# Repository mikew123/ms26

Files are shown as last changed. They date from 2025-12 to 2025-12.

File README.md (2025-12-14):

# ms26
Mini Sumo DIY for Spring 2026 RoboRama.<br>
This is a DIY mini sumo 10cmx10cm robot made with 3D printed body with mounts and "off the shelf" modules and a point to point wired 0.1" bread board to connect it all together.<br>

# Mechanics
## Body
The body is in 2 parts printed on 3D printer, a main body and a top lid and is created using Matte Black PLA filiment.<br>
The main body is one piece and has mounts for the motors/wheels and the circuit board and sensors. There is an opening on the side for the battery to be inserted.<br>
The top lid bolts onto the body and has compartments to put pennys in as weights, there is also a cover to tightly hold the pennys in place.<br>
3D design using FreeCad:<br>
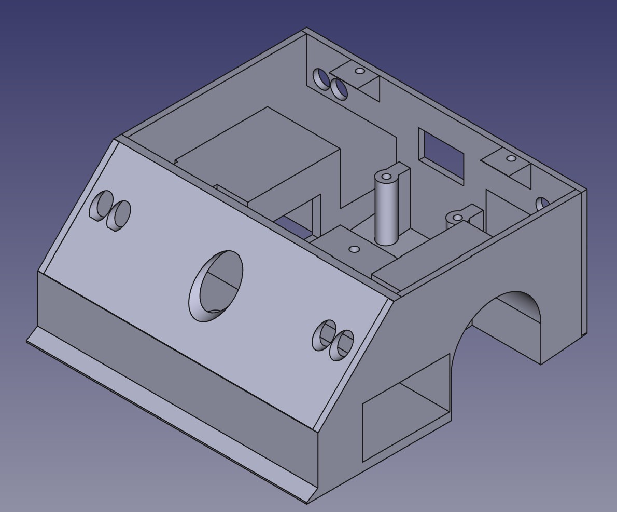
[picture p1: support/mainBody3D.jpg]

The final mini-sumo robot without the lid<br>
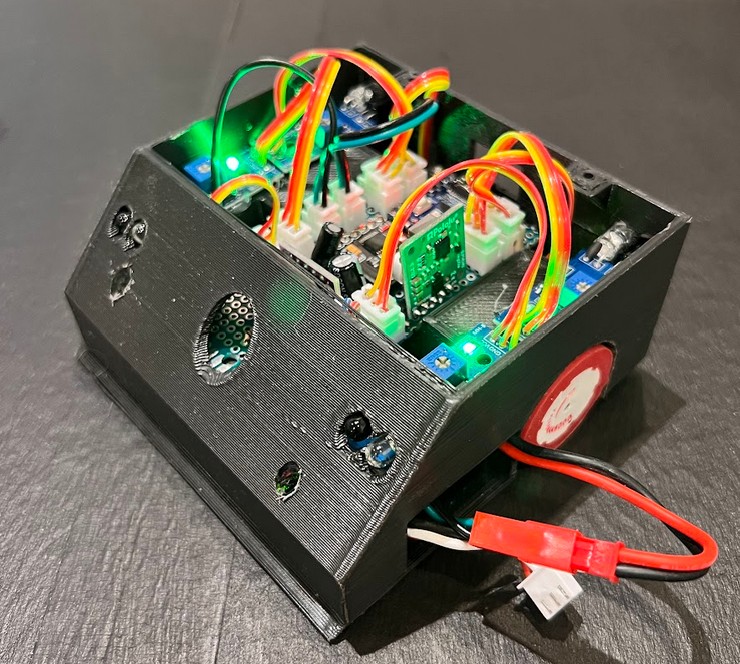
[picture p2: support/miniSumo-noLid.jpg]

The object and edge sensors are mounted as well as wheels and motors. The motors are bolted into place using a 3D saddle mount<br>
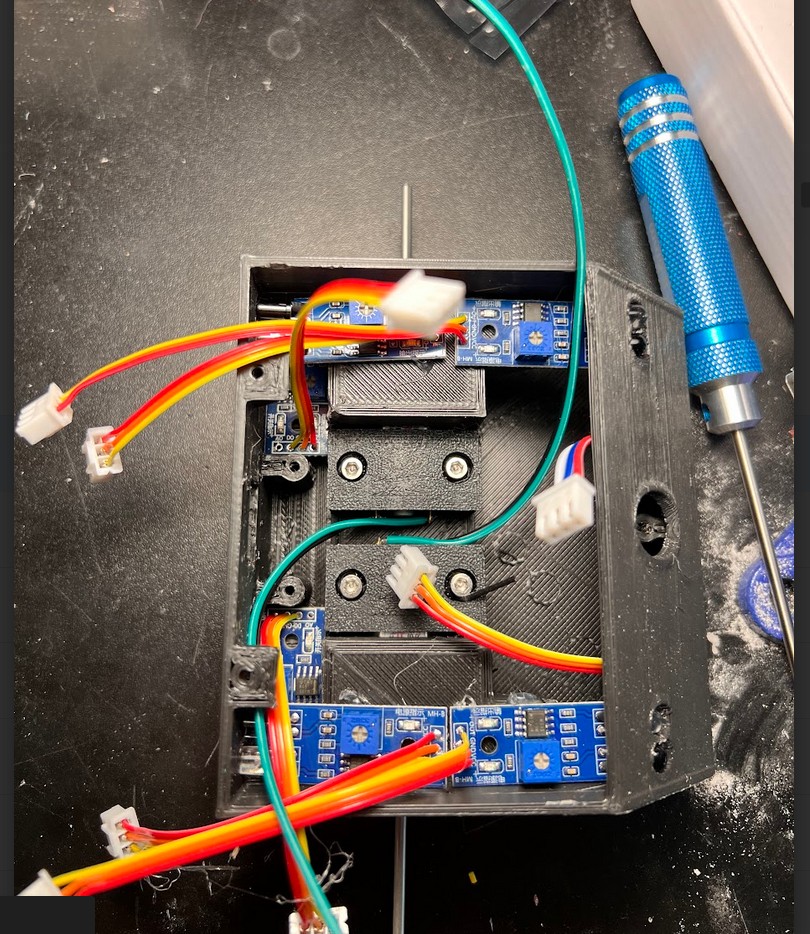
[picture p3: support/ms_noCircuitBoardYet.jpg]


## Weight
The weight limit is 500 grams. Without a lid it weighs in at about 225 grams.
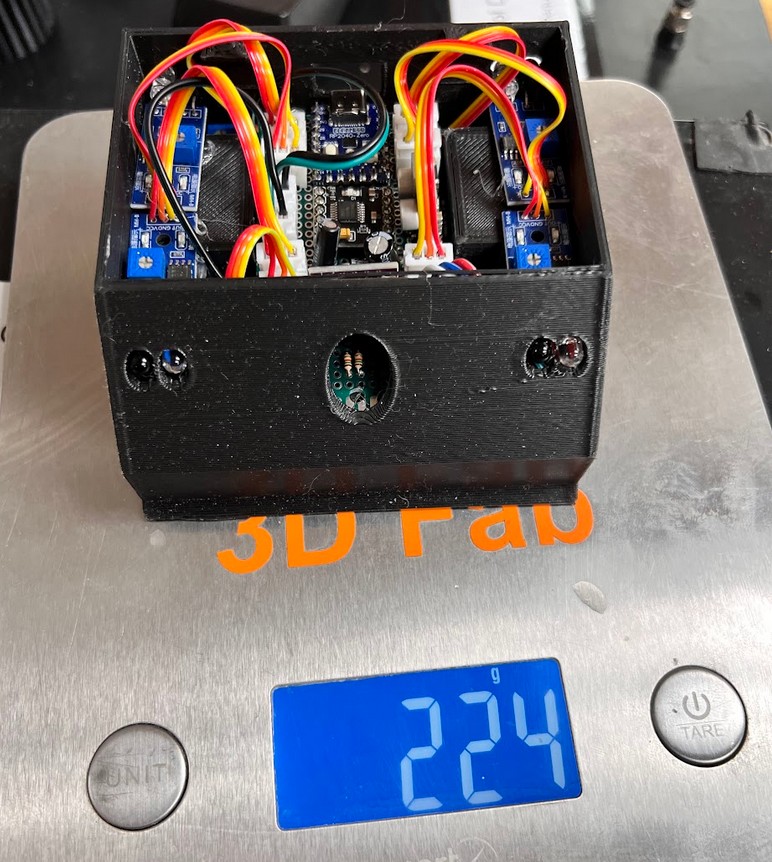
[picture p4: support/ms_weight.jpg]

Hmmm the coffee shop weighed it as 295!!
## Motor
FingerTech "Silver Spark" 16mm Gearmotor 50:1<br>
<https://www.fingertechrobotics.com/proddetail.php?prod=ft-Sspark16><br>

## Wheel
FingerTech Mini-Sumo Wheels (pair)<br>
<https://www.fingertechrobotics.com/proddetail.php?prod=ft-minisumo-wheels-1125><br>
The wheels and motors are made to be used together for the 10cm width on mini-sumo.<br>
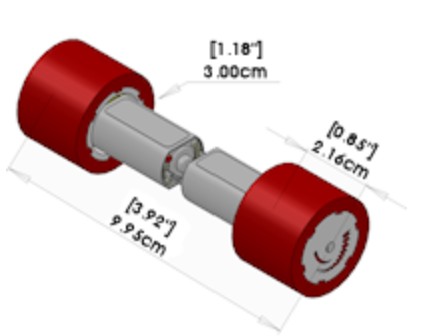
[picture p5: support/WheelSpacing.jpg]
<br>

## Battery
Amazon Blomiky 7.4V 1200mAH Lipo Battery Pack with JST Plug<br>
<https://www.amazon.com/dp/B07DB52T49?ref=ppx_yo2ov_dt_b_fed_asin_title><br>
The battery can run for hours and supplys a lot of the weight.<br>

# Circuit modules
## Processor
Waveshare RP2040-Zero, a Pico-like MCU Board Based on Raspberry Pi MCU RP2040, Mini ver<br>
<https://www.waveshare.com/rp2040-zero.htm><br>
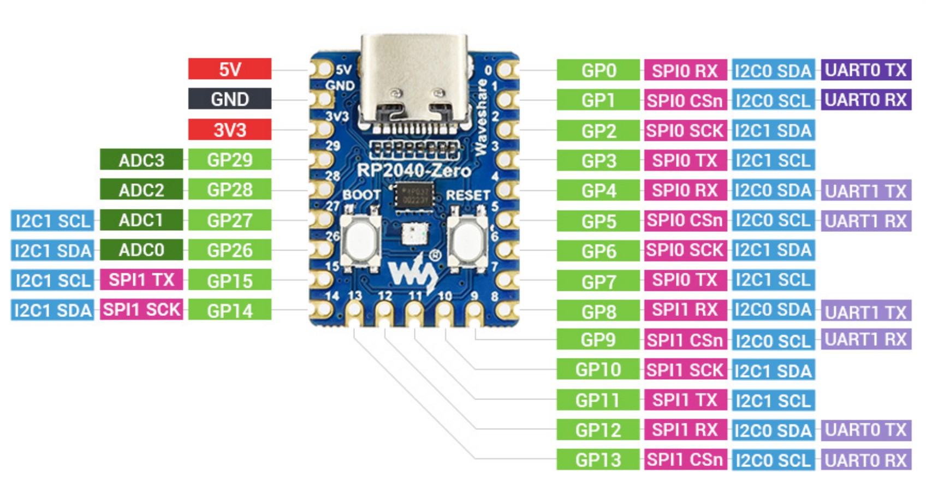
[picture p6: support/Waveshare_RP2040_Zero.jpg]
<br>

## 6V regulator
Pololu 6V, 2.7A Step-Down Voltage Regulator D36V28F6</br>
<https://www.pololu.com/product/3783><br>
This supplies power for the processor and 3.3V regulator. The 6V output allows a protection diode while keeping the voltage above 5V</br>

## 3.3V regulator
SparkFun BabyBuck Regulator Breakout - 3.3V (AP63203)<br>
<https://www.sparkfun.com/sparkfun-babybuck-regulator-breakout-3-3v-ap63203.html><br>
This supplies 3.3V power to the sensors. The 3.3v from the RP2040 module does not have the current rating for the sensors.<br>
The voltage is enabled using a pin on the RP2040.<>

## Motor driver
Amazon DRV8833 DC Motor Driver Controller Board 1.5A Dual H Bridge<br>
<https://www.amazon.com/dp/B0DB8CX8LK?ref=ppx_yo2ov_dt_b_fed_asin_title><br>
The motor speed is controlled using this PWM library <https://github.com/khoih-prog/RP2040_PWM><br>
The driver is enabled using a pin on the RP2040.<br>

## TOF Range sensor
Adafruit VL6180X Time of Flight Distance Ranging Sensor (VL6180) - STEMMA QT<br>
<https://www.adafruit.com/product/3316><br>
Library <https://github.com/adafruit/Adafruit_VL6180X><br>

## Edge detector
Amazon TCRT5000 Infrared Reflective Sensor IR Photoelectric Switch Barrier Line Obstacle Avoidance Module<br>
<https://www.amazon.com/dp/B08YRCR6ML?ref=ppx_yo2ov_dt_b_fed_asin_title>

## Object detector
Amazon IR Infrared Obstacle Avoidance Sensor Module 2-30cm Adjustable 3.3V-5V 3-Wire Detection <br>
<https://www.amazon.com/dp/B0FR4MZFMH?ref=ppx_yo2ov_dt_b_fed_asin_title><br>

## IMU
Amazon LSM6DS3 6-axis IMU 3-axis Accelerometer 3-axisGyroscope Sensor 6 Degrees of Freedom,Embedded Temperature Sensor, SPI I2C<br>
<https://www.amazon.com/dp/B0DGQ9533D?ref=ppx_yo2ov_dt_b_fed_asin_title><br>
Library <https://docs.arduino.cc/libraries/arduino_lsm6ds3/> <br>
The library only uses I2C0 (Wire) with a fixed address (not same as the TOF sensor) and fixed update rate of 104 Hz.<br>

# Circuit board
The circuit board is a 0.1" perf board and is point to point wired. The sensors and motor are connected using locking connectors and the battery wire with a connector on the end is soldered on.<br>
The battery is managed by reading its voltage on one of the analog A/D input pins using a voltage divider to keep the voltage on the piins less than 3.3V. The 3.3V regulator and motor driver are disabled when the battery voltage is less than 6.6V.<br>
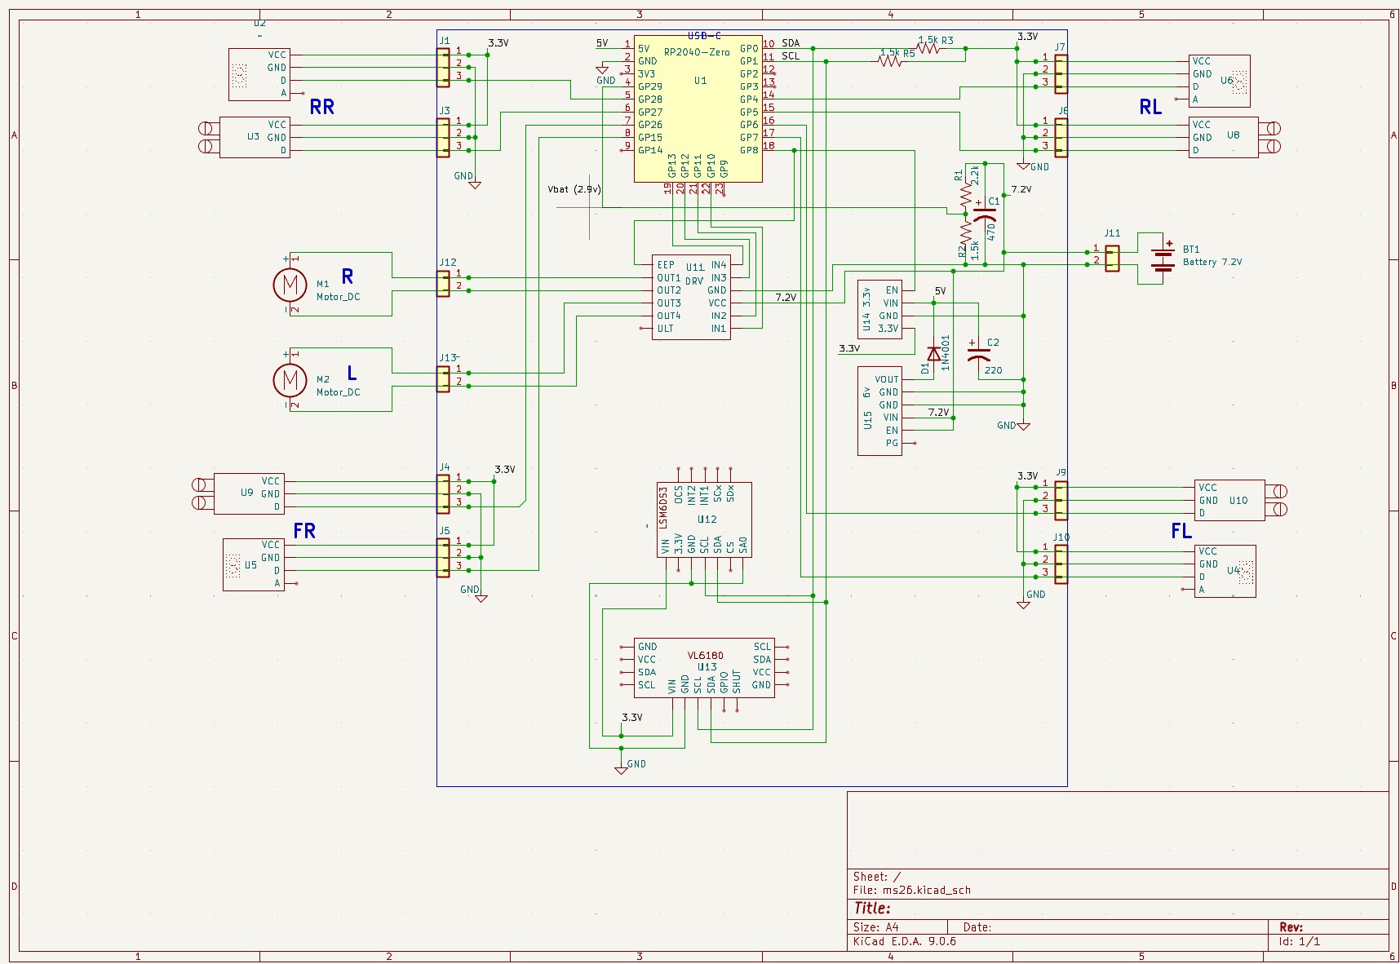
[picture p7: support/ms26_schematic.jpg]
<br>

# Mini Sumo Movement
The basic strategy is to move between the edges of the ring and push the opponent off the ring when contacted.<br>
The motor is geared and has lots of torque for the small motor. The wheels have a lot of surface area and made of silicon giving them a lot of traction. The speed is at 100% when moving edge to edge providing a lot of momentum.<br>
The bottom sensors on the front sense the edge of the ring and cause the robot to spin around about 180 deg before driving to the edge again.<br>
<br>
The front TOF sensor has two purposes:<br>
- Start/Stop switch<br>
    To start or stop a finger is held over the sensor hole for at least a second and the action begins when the finger is removed. The start action actually starts a 5 second timer before the robot starts moving as required.<br>
- Object detection<br>
    When an object is detected in front (hopefully the competitor) the robot makes sure both bottom front edge detectors are tripped before reversing and spinning.<br>
<br>

The front sensors on the left and right cause the robot to steer right or left to enable pushing the opponent better by trying to move to its center.<br> 

# Code
The RP2040 code in C++ is developed using the Arduino IDE and uses both cores. C++ allows extremely fast sensor detection and wheel speed changes of a few thousand per second. To allow the fast edge detection and response the TOF sensor library is a bit slow and seems to only be blocking so it was moved to the 2nd core along with the IMU which shares the I2C bus. A simple FIFO sends the TOF and IMU information to the main core.<br>

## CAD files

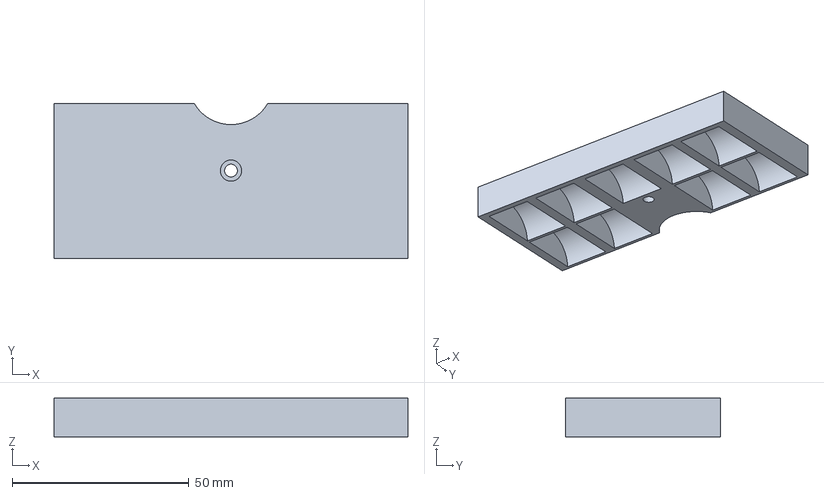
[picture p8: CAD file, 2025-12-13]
3d/MS26-topCap.3mf
100.0 x 43.9 x 11.0 mm

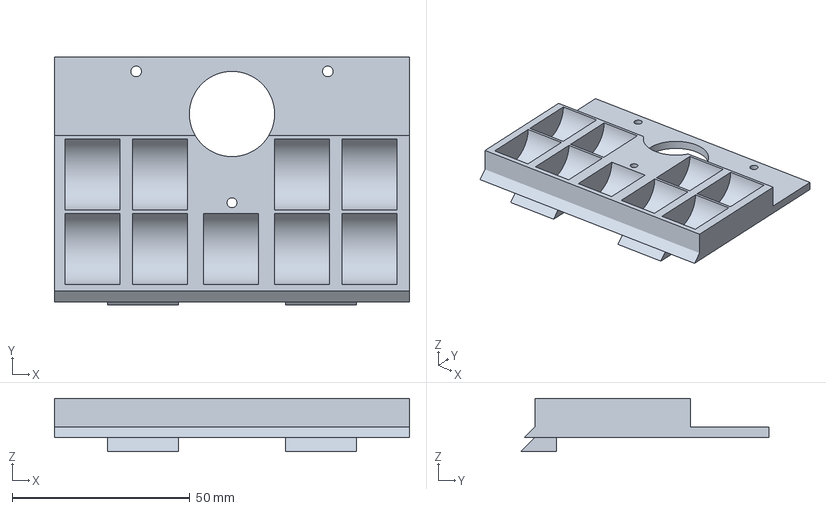
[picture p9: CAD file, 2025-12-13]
3d/MS26-top.3mf
100.0 x 69.8 x 15.0 mm

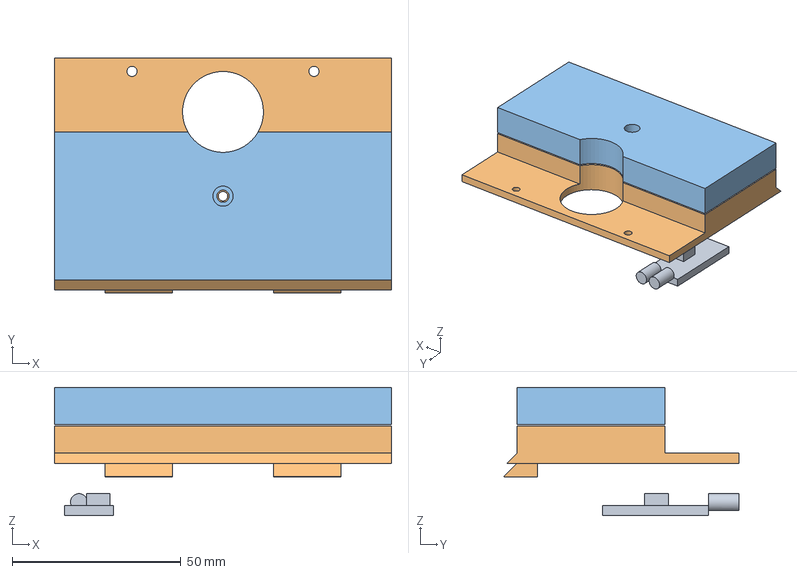
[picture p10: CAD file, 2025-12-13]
3d/MS26.FCStd
100.0 x 69.8 x 38.0 mm
ObSensRR
top
topCap

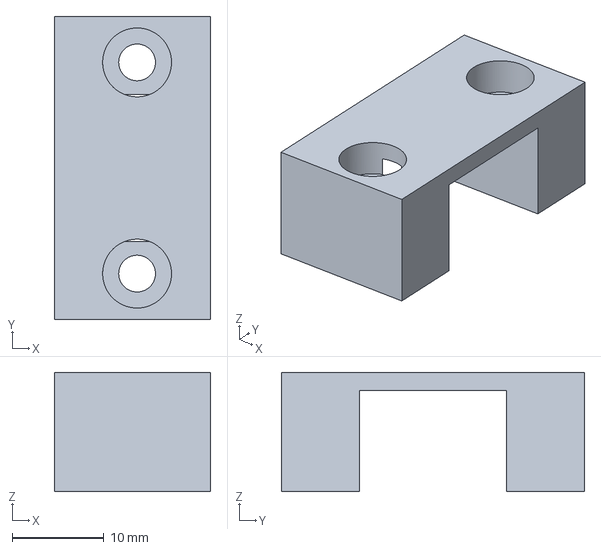
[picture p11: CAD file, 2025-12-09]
3d/MS26-MotorClampR.3mf
17.0 x 33.0 x 13.0 mm

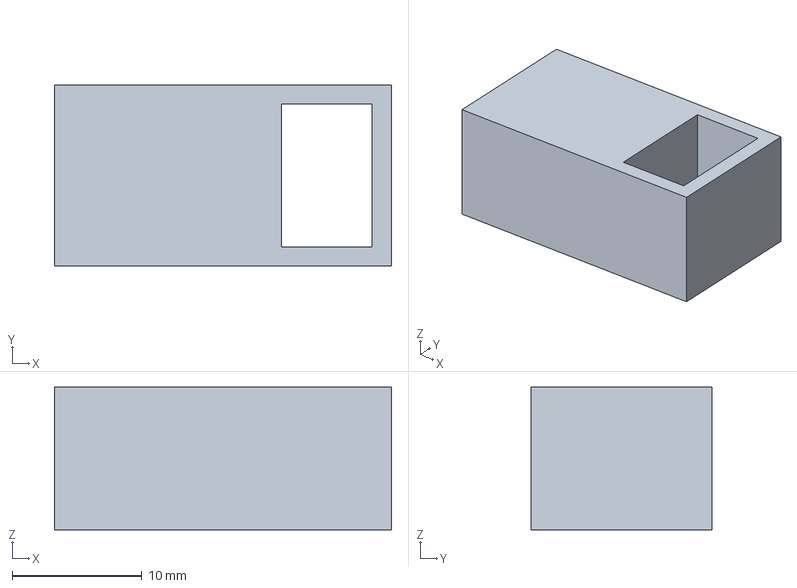
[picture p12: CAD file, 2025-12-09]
3d/MS26-test1.3mf
26.0 x 14.0 x 11.0 mm

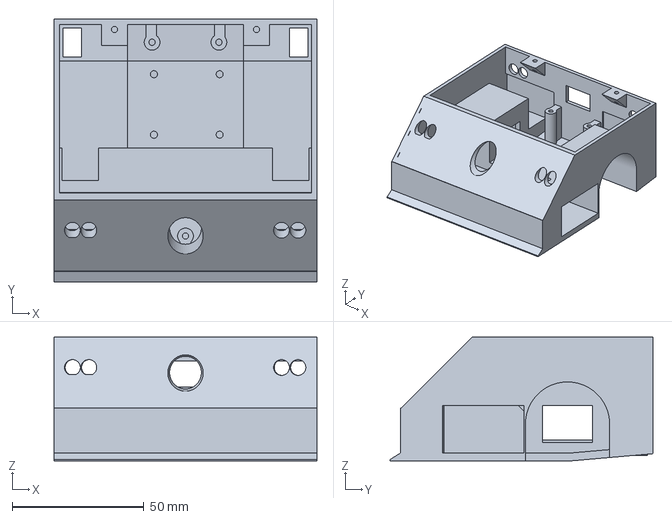
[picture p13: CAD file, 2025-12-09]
3d/MS26-Body.3mf
100.0 x 100.0 x 47.0 mm

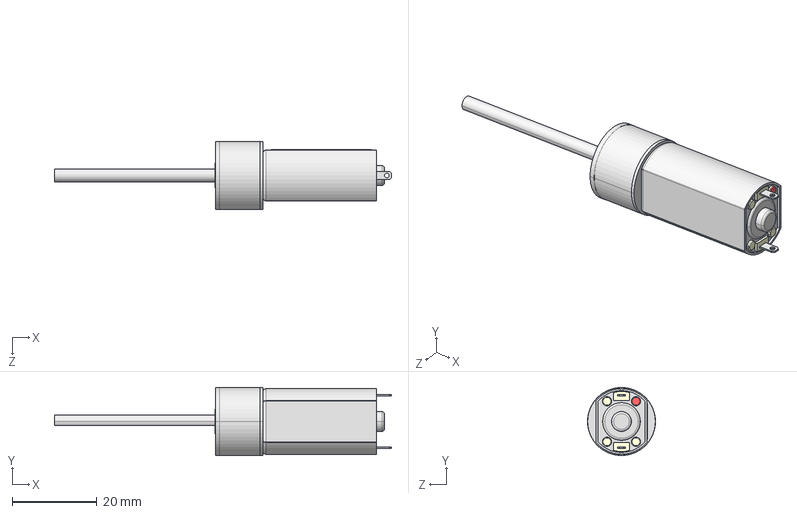
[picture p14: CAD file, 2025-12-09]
3d/FingerTech_Silver_Spark_223350.STEP
79.7 x 16.1 x 16.1 mm

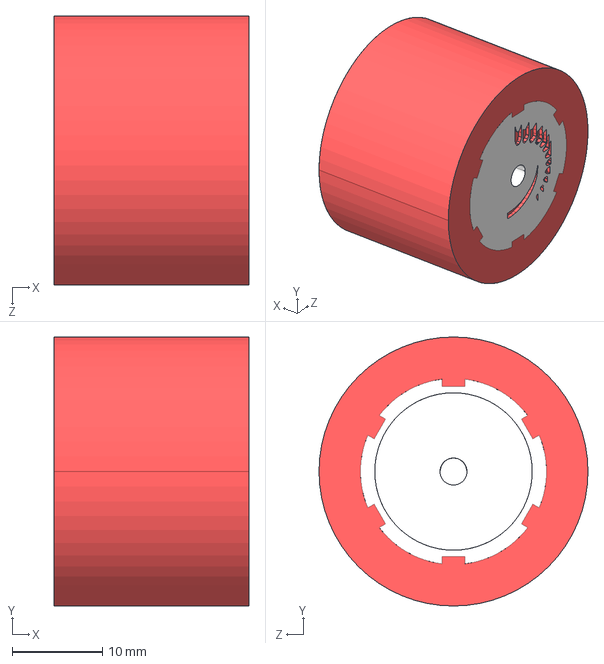
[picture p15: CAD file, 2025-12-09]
3d/MiniSumo_wheel_1125.IGS
21.6 x 29.8 x 29.8 mm

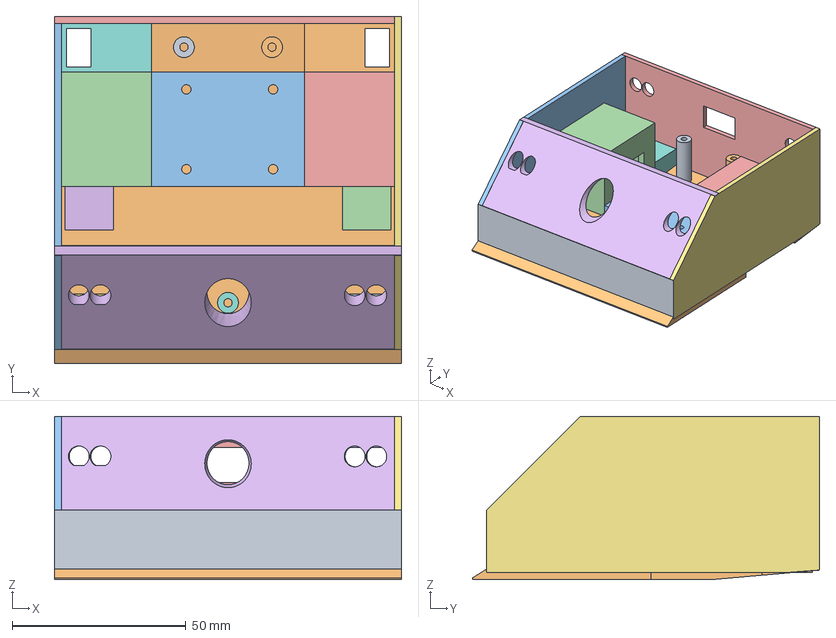
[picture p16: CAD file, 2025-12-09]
3d/MS26_bak.FCStd
100.0 x 100.0 x 47.0 mm
FrontVert
bottom
RightSide
masterWheelWellR
cloneWheelCutoutL
masterObSensSupportR
masterLineSensorMountFR
cloneLineSensorMountRR
cloneLineSensorMountFL
cloneLineSensorMountRL
MotorMountPlate
cloneObSensSupportL
Rear
FrontSlope
LeftSide
masterBoardMountF
cloneBoardMountRR
cloneBoardMountRL

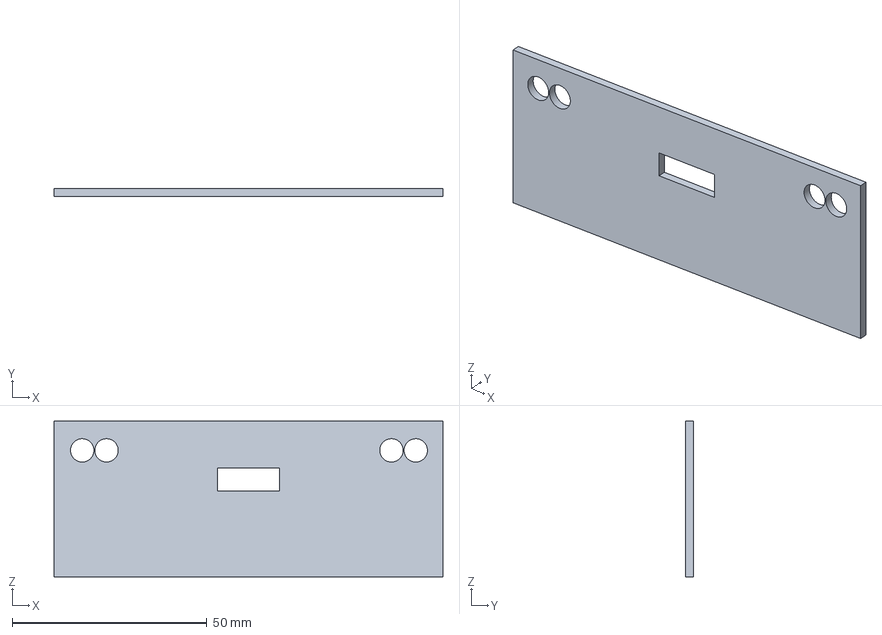
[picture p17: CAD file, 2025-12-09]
3d/MS26-test2.3mf
100.0 x 2.00 x 40.0 mm

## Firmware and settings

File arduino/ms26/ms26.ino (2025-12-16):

#include <Wire.h>
#include <SPI.h>

// #include <utility/imumaths.h>

#include <Adafruit_NeoPixel.h>
#include "RP2040_PWM.h"
#include "Adafruit_VL6180X.h"
#include <Arduino_LSM6DS3.h>
#include <atomic>

// On board RGB LED 
#define NEO 16

// GPIO PINS
#define SDA0 0
#define SCL0 1

#define LINRL_PIN 4
#define OBSRL_PIN 5
#define OBSFL_PIN 6
#define LINFL_PIN 7

#define VREG_EN   8

#define PIN_MOTOR_L1      10
#define PIN_MOTOR_L2      11
#define PIN_MOTOR_R1      12
#define PIN_MOTOR_R2      13

#define LINFR_PIN 15
#define OBSFR_PIN 26
#define OBSRR_PIN 27
#define LINRR_PIN 28

#define VBAT_PIN  29

// 2nd core interprocess stuff
volatile std::atomic<bool> core1InitBasicsFinished = false;
volatile std::atomic<bool> core2InitFinished = false;
volatile std::atomic<bool> core2CalImu = false;

// buffer TOF range data for inter-process transfer
#define TOFSTRUCT_LEN 2
volatile uint8_t tofStructWrIdx = 0;
volatile uint8_t tofStructRdIdx = 0;
volatile std::atomic<uint8_t> tofStructCnt = 0;
volatile struct {
  uint8_t range = 255;
} tofStruct[TOFSTRUCT_LEN];

// buffer IMU data for inter-process transfer
#define IMUSTRUCT_LEN 2
volatile uint8_t imuStructWrIdx = 0;
volatile uint8_t imuStructRdIdx = 0;
volatile std::atomic<uint8_t> imuStructCnt = 0;
volatile struct {
  float yaw    = 0; // continuous angular rotation in degrees (integrate ang vel)
  float tiltFB = 0; // +front or -back tilt, real time
  float tiltRL = 0; // +right or -left tilt, real time
  float hitMax = 0; // any angle hit detection, abs acceleration max
} imuStruct[IMUSTRUCT_LEN];


///////////////// On Board LED ////////////////////////////
// Create led instance
Adafruit_NeoPixel neo(1, NEO, NEO_GRB + NEO_KHZ800);

bool neoRed   = 0;
bool neoGreen = 0;
bool neoBlue  = 0;

// update the RGB colors on the built in NEO LED
// Only updates when colors change
void setNeo(int r=0, int g=150, int b=0) {
  if(r!=neoRed | g!=neoGreen | b!=neoBlue) {
    neoRed   = r;
    neoGreen = g;
    neoBlue  = b;
    neo.clear();
    neo.setPixelColor(0, neo.Color(r, g, b));
    neo.show();   // Send the updated pixel colors to the hardware.
  }
}


void InitNeo(int r=0, int g=150, int b=0) {
  neo.begin();
  setNeo();
}

///////////// Wheel motors ///////////////////
//creates pwm instance for motor drive
RP2040_PWM* PWM_MOTOR_L1;
RP2040_PWM* PWM_MOTOR_L2;
RP2040_PWM* PWM_MOTOR_R1;
RP2040_PWM* PWM_MOTOR_R2;

// Motor PWM motorPwmFreq
float motorPwmFreq = 5000;

void InitMotorDrivers(){
  // initialize to stop-braked (100PCT FOR STOP BRAKED)
  PWM_MOTOR_L1 = new RP2040_PWM(PIN_MOTOR_L1, motorPwmFreq, 100);
  PWM_MOTOR_L2 = new RP2040_PWM(PIN_MOTOR_L2, motorPwmFreq, 100);
  PWM_MOTOR_R1 = new RP2040_PWM(PIN_MOTOR_R1, motorPwmFreq, 100);
  PWM_MOTOR_R2 = new RP2040_PWM(PIN_MOTOR_R2, motorPwmFreq, 100);
}

// +pct = fwd, -pct = rev, 0pct = stop-braked
// pct limited to +-100%
//void MotorDrivePct(int pctL, int pctR) {
void MotorDrivePct(float pctL, float pctR) {
  pctL = -pctL; // opposite rotation as Right Wheel
  // Limit to +-100 pct
  if(pctL>100) pctL=100;
  if(pctL<-100) pctL=-100;
  if(pctL>=0) {
    // Motor Left Forward
    PWM_MOTOR_L1->setPWM(PIN_MOTOR_L1, motorPwmFreq, 100);
    PWM_MOTOR_L2->setPWM(PIN_MOTOR_L2, motorPwmFreq, 100-pctL);
  } else {
    // Motor Left Reverse
     PWM_MOTOR_L1->setPWM(PIN_MOTOR_L1, motorPwmFreq, 100+pctL);
     PWM_MOTOR_L2->setPWM(PIN_MOTOR_L2, motorPwmFreq, 100);
  }

  pctR = +pctR;
  // Limit to +-100 pct
  if(pctR>100) pctR=100;
  if(pctR<-100) pctR=-100;
  if(pctR>=0) {
    // Motor Right Forward
    PWM_MOTOR_R1->setPWM(PIN_MOTOR_R1, motorPwmFreq, 100);
    PWM_MOTOR_R2->setPWM(PIN_MOTOR_R2, motorPwmFreq, 100-pctR);
  } else {
    // Motor Right Reverse
    PWM_MOTOR_R1->setPWM(PIN_MOTOR_R1, motorPwmFreq, 100+pctR);
    PWM_MOTOR_R2->setPWM(PIN_MOTOR_R2, motorPwmFreq, 100);
  }

}

/////////////// I2C ///////////////////////////
void Core2_InitI2c(int hz = 100000) {
  Wire.setClock(hz);
  Wire.setSCL(SCL0);
  Wire.setSDA(SDA0);
  Wire.begin();
}

/////////////// TOF sensor ////////////////////
// TOF sensor read and processed in core 2
Adafruit_VL6180X vl = Adafruit_VL6180X();

void Core2_InitTof() {
  Serial.println("Adafruit VL6180x TOF sensor init");
  if (! vl.begin(&Wire)) {
    Serial.println("Failed to find TOF sensor");
    while (1);
  }
  Serial.println("TOF sensor found!");
  for(int i=0; i<TOFSTRUCT_LEN; i++) {
    tofStruct[i].range = 255;
  }
  tofStructCnt = 0; /* atomic */
  tofStructWrIdx = tofStructRdIdx = 0;
}

// Put TOF sensor range values value into the buffer
void Core2_GetTofSensor() {
  uint8_t range  = vl.readRange(); /* blocking */
  uint8_t status = vl.readRangeStatus();
  // if(status==0) Serial.println(range);
  // else Serial.println("---");
  if(status != 0) range = 255;
  // wait for buffer not full - core1 needs to read a value
  // TODO: timeout?
  while(tofStructCnt>=TOFSTRUCT_LEN){
    Serial.println("TOF struct full - can't write new value");
    delay(100);
  }
  // Pass TOF data to core1
  tofStruct[tofStructWrIdx].range = range;
  tofStructCnt++; /* atomic */
  if(tofStructWrIdx<TOFSTRUCT_LEN) tofStructWrIdx++;
  else tofStructWrIdx = 0;
}

uint8_t currentRange = 255;
// get current (or last) range in mm (typ 0 to 200), 255 if no range detected
// range value is saved in global variable
bool GetTofData(){
  if(tofStructCnt>0){
    currentRange = tofStruct[tofStructRdIdx].range;
    tofStructCnt--; /* atomic */
    if(tofStructRdIdx<TOFSTRUCT_LEN) tofStructRdIdx++;
    else tofStructRdIdx = 0;
    return true;
  } 
  return false;
}

/////////////////// IMU ////////////////////////
// IMU read and processed in core 2
// The IMU is instanced in the class - there can only be 1
// Calibration offsets created during init
float ax0=0;
float ay0=0;
float az0=0;
float gx0=0;
float gy0=0;
float gz0=0;
#define IMU_CAL_CNT 100
#define IMU_DIS_CNT 100

uint32_t lastYawMillis = 0;
float imuYaw = 0.0;

void Core2_CalImuOffsets() {
  // discard some readings to clear out whatever
  float x, y, z;
  for(int i=0;i<IMU_DIS_CNT;i++){
    if (IMU.gyroscopeAvailable()) {
      IMU.readGyroscope(x, y, z);
    }
  }

  // Average lots of readings to cal offsets
  gx0=0;
  gy0=0;
  gz0=0;
  int cnt = 0;
  while(cnt<IMU_CAL_CNT) {
    if (IMU.gyroscopeAvailable() && IMU.accelerationAvailable()) {
      IMU.readGyroscope(x, y, z);
      gx0+=x;
      gy0+=y;
      gz0+=z;
     IMU.readAcceleration(x, y, z);
      ax0+=x;
      ay0+=y;
      az0+=z;
      cnt++;
    }
  }
  gx0/=IMU_CAL_CNT;
  gy0/=IMU_CAL_CNT;
  gz0/=IMU_CAL_CNT;
  ax0/=IMU_CAL_CNT;
  ay0/=IMU_CAL_CNT;
  az0/=IMU_CAL_CNT;

  // reset IMU yaw integration
  imuYaw = 0.0;
}

void Core2_InitImu() {
  Serial.println("IMU Sensor Test"); Serial.println("");

  /* Initialise the sensor */
  if (!IMU.begin()) {
    Serial.println("Failed to initialize IMU!");
    return; //while (1);
  }

  Serial.print("Gyroscope sample rate = ");
  Serial.print(IMU.gyroscopeSampleRate());
  Serial.println(" Hz");

  Core2_CalImuOffsets();

  // initialize IMU data buffer
  imuStructCnt = 0; /* atomic */
  imuStructWrIdx = imuStructRdIdx = 0;
}

void Core2_ProcImu() {
  if (IMU.accelerationAvailable() && IMU.gyroscopeAvailable()) {
//    return;

    float ax, ay, az;
    float gx, gy, gz;

    IMU.readAcceleration(ax, ay, az);
    ax -= ax0;
    ay -= ay0;
    az -= az0;
    // Serial.print(ax);
    // Serial.print('\t');
    // Serial.print(ay);
    // Serial.print('\t');
    // Serial.print(az);

    IMU.readGyroscope(gx, gy, gz);
    gx -= gx0;
    gy -= gy0;
    gz -= gz0;

    // Tilt detection degrees using acceleration (gravity)
    float tiltFB = 180*asin(az)/3.14;
    float tiltRL = 180*asin(ax)/3.14;
    float hitMax = fabs(ax);
    if(fabs(ay)>hitMax) hitMax = fabs(ay);
    if(fabs(az)>hitMax) hitMax = fabs(az);


    // Integrate angular velocity to get yaw
    // TODO: Use usec time?
    uint32_t currentMillis = millis();
    float dt = (currentMillis - lastYawMillis)/1000.0;
    lastYawMillis = currentMillis;
    if(dt<100) {
      // seems valid time difference perform integration
      imuYaw += dt*gy;
      // save into buffer for core1
      if(imuStructCnt < IMUSTRUCT_LEN) {
        imuStruct[imuStructWrIdx].yaw    = imuYaw;
        imuStruct[imuStructWrIdx].tiltFB = tiltFB;
        imuStruct[imuStructWrIdx].tiltRL = tiltRL;
        imuStruct[imuStructWrIdx].hitMax = hitMax;
        imuStructWrIdx++;
        if(imuStructWrIdx >= IMUSTRUCT_LEN) imuStructWrIdx = 0;
        imuStructCnt++;
      }
    }

    // Serial.print('\t');
    // Serial.print(gx);
    // Serial.print('\t');
    // Serial.print(gy);
    // Serial.print('\t');
    // Serial.print(gz);
    // Serial.print('\t');
    // Serial.print(tiltFB);
    // Serial.print('\t');
    // Serial.print(tiltRL);
    // Serial.print('\t');
    // Serial.print(hitMax);
    // Serial.print('\t');
    // Serial.print(imuYaw);
    // Serial.println();
  }
}

float currentYaw    = 0.0;
float currentTiltFB = 0.0;
float currentTiltRL = 0.0;
float currentHitMax = 0.0;
// Get IMU data from core2
void GetImuData(){
  if(imuStructCnt > 0){
    currentYaw    = imuStruct[imuStructRdIdx].yaw;
    currentTiltFB = imuStruct[imuStructRdIdx].tiltFB;
    currentTiltRL = imuStruct[imuStructRdIdx].tiltRL;
    currentHitMax = imuStruct[imuStructRdIdx].hitMax;
    imuStructRdIdx++;
    if(imuStructRdIdx >= IMUSTRUCT_LEN) imuStructRdIdx = 0;
    imuStructCnt--;
  }
}

////////////////////// IR detectors ////////////////

void InitIRdet() {
  pinMode(LINFR_PIN, INPUT);
  pinMode(LINFL_PIN, INPUT);
  pinMode(LINRR_PIN, INPUT);
  pinMode(LINRL_PIN, INPUT);
  pinMode(OBSFR_PIN, INPUT);
  pinMode(OBSFL_PIN, INPUT);
  pinMode(OBSRR_PIN, INPUT);
  pinMode(OBSRL_PIN, INPUT);
}

int16_t GetIRdet() {
  int16_t det = 0;
  det |= digitalRead(OBSFR_PIN)<<0;
  det |= digitalRead(OBSFL_PIN)<<1;
  det |= digitalRead(OBSRR_PIN)<<2;
  det |= digitalRead(OBSRL_PIN)<<3;
  det |= digitalRead(LINFR_PIN)<<8;
  det |= digitalRead(LINFL_PIN)<<9;
  det |= digitalRead(LINRR_PIN)<<10;
  det |= digitalRead(LINRL_PIN)<<11;
  return(det);
}

///////////////// 3.3V VREG /////////////////////
void VregEnable(bool on=true) {
  digitalWrite(VREG_EN, on);
  delay(10);
}

void InitVreg() {
  pinMode(VREG_EN, OUTPUT);
  VregEnable(true);
}

/////////////// VBAT measurement ////////////////
#define VBAT_MIN 2*3.3
#define VBAT_PIN_MAX 1023
#define VBAT_SCALE (3.3/(15.0/(22+15)))*(6.5/6.6)

void InitVbatMeas() {

}

float GetVbat() {
  int vbatPinValue = analogRead(VBAT_PIN);
  float vbat = vbatPinValue/float(VBAT_PIN_MAX) * VBAT_SCALE;
  return(vbat);
}

/////////////// Sensors /////////////////

#define FSM_TOF_MIN_RANGE  12
#define FSM_FWD_SPEED      100
#define FSM_REV_SPEED      FSM_FWD_SPEED
#define FSM_SPIN_SPEED     FSM_FWD_SPEED
#define FSM_MAX_SPIN_TIME  1.5*((25*1000)/FSM_SPIN_SPEED)
#define FSM_SPIN_ANGLE     100.0
#define FSM_BACKUP_TIME    ((25*500)/FSM_REV_SPEED)
#define FSM_TRIG_DET_TIME  1000 /* 1 second trigger "filter" to minimize random stops */
#define FSM_START_DELAY    5000 /* 5 sec time before starting movement */

/////////////////////// FSM for movement /////////////////////

enum fsmState{
INIT, IDLE0, IDLE1, WAIT_START, 
FWD, BACKUP, SPIN, BACKUP2, SPIN2
};


struct {
  // trigger input
  bool trig = false;
  // edge sensors
  bool esFR = false;
  bool esFL = false;
  bool esRR = false;
  bool esRL = false;
  bool es34 = false; // 3 or 4 edge sensors tripped, must not be on black arena
  // object sensors
  uint8_t range = 0; // Front Center TOF sensor
  bool osFC = false;
  bool osFR = false;
  bool osFL = false;
  bool osRR = false;
  bool osRL = false;
  // spin direction +/- latched based on edge sensor
  int spinDir = 0; 
  // yaw value when SPIN begins - used to measure SPIN angle
  float yaw0 = 0.0;
  // state timer
  uint32_t timer = 0;
  // state info
  fsmState currentState = INIT;
  fsmState nextState = IDLE0;
} fsmData;

// Set the sensor data in the global FSM data structure
void setFsmSensorData(uint8_t range, uint16_t det) {
  static uint32_t timer = 0;
  fsmData.range = range;
  // edge sensors
  fsmData.esFR = det&0x0100;
  fsmData.esFL = det&0x0200;
  fsmData.esRR = det&0x0400;
  fsmData.esRL = det&0x0800;
  // object sensors
  fsmData.osFC = range!=255 && range>=FSM_TOF_MIN_RANGE; // 255 is no det
  fsmData.osFR = det&0x0001;
  fsmData.osFL = det&0x0002;
  fsmData.osRR = det&0x0004;
  fsmData.osRL = det&0x0008;

  // 3 or 4 edge sensors tripped, not on black arena
  int cnt = 0;
  if(fsmData.esFR) cnt++;
  if(fsmData.esFL) cnt++;
  if(fsmData.esRR) cnt++;
  if(fsmData.esRL) cnt++;
  fsmData.es34 = (cnt >= 3);

  // set spin direction based on the edge sensor tripped
  if     (fsmData.esFR) fsmData.spinDir = +1;
  else if(fsmData.esFL) fsmData.spinDir = -1;
  else if(fsmData.esRR) fsmData.spinDir = +1;
  else if(fsmData.esFL) fsmData.spinDir = -1;

  // trigger on range < min ie. finger covers FC sensor hole
  // this could help false triggers stopping the motion
  // trigger is set when range<min for 1 sec and then 255
  // reset timer when range > min including 255
  if(range>=2*FSM_TOF_MIN_RANGE) {
    // finger not covering TOF hole
    fsmData.trig = false;
    timer = millis();
  }
  else if(range<FSM_TOF_MIN_RANGE){
    // finger is covering TOF hole
    if(!fsmData.trig && ((millis() - timer) >= FSM_TRIG_DET_TIME)) {
      fsmData.trig = true;
    }
  }
}

void fsm(float &wheelR, float &wheelL) {
  static bool lastTrig = false;
  static bool esFR_latch = false;
  static bool esFL_latch = false;
  bool trig0 = false;
  bool trig1 = false;
  // set triggers when trig value changes
  if(fsmData.trig != lastTrig) {
    trig1 = fsmData.trig; // finger on FC
    trig0 = !fsmData.trig; // finger off FC
  }
  lastTrig = fsmData.trig;

  int fwdTime;

  int r = 100*(fsmData.esFR|fsmData.esFL|fsmData.esRR|fsmData.esRL);
  int g = 100*(fsmData.osFR|fsmData.osFL|fsmData.osRR|fsmData.osRL);
  int b = int(100*((200-fsmData.range)/200.0));
  if (b<0) b=0;

  // default motor-wheel speed 0 percent
  wheelR = 0;
  wheelL = 0;

  static int es34Cnt = 0;
  if(fsmData.es34) {
    // 3 or 4 edge sensors tripped, must NOT be in arena
    es34Cnt++;
    if(es34Cnt>=100) {
      fsmData.nextState = IDLE0;
    }
  }
  else es34Cnt = 0;

  bool stateChange = false;
  if(fsmData.nextState != fsmData.currentState) {
    stateChange = true;
  }
  fsmState state = fsmData.nextState;
  fsmState nextState = state; // default no state change

  // FSM
  switch(state) {
    case IDLE0: 
      // wait for finger on FC before start sequence
      if(trig1) {
        nextState = IDLE1;
      }
      // continuous show sensor status
      setNeo(r,g,b);
      break;

    case IDLE1: 
      if(stateChange) {
        setNeo(0,0,255); // BLUE
      }
      // wait for finger is off the FC to start delay before moving
      if(trig0) {
        nextState = WAIT_START;
      }
      break;

    case WAIT_START: 
      if(stateChange) {
        // wait before moving
        fsmData.timer = millis()+FSM_START_DELAY;
        // calibrate IMU on the mat
        core2CalImu = true;
        setNeo(255,0,0); // RED
      }

      if(trig1) {
        // stop and return to idle when finger on fc
        nextState = IDLE0;
      }
      else if(millis() >= fsmData.timer) {
        nextState = FWD;
      }
      break;
    
    case FWD: 
      if(stateChange) {
        fsmData.timer = millis();
        esFR_latch = false;
        esFL_latch = false;
        setNeo(0,255,0); // GREEN
      }
      // Get a mount of time after FWD started
      fwdTime = millis() - fsmData.timer;
      // latch front edge sensors
      esFR_latch |= fsmData.esFR;
      esFL_latch |= fsmData.esFL;

      if(trig1) {
        // stop and idle when finger on FC
        nextState = IDLE0;
      }
      else if(fwdTime>3000) {
        // taking too long the robots must be tied - SPIN to break hold
        wheelR = FSM_FWD_SPEED;
        wheelL = FSM_FWD_SPEED;
        nextState = SPIN;
      }
      else if((currentTiltFB>10)&&(fwdTime>=500)) {
        // Ingnore lift sensors when initialy accelerating forward
        // Front lift detection - opponent in front got under robot
        // NOTE: front TOF sensor is not reliable enough to ensure it is in front
        // backup then spin
        wheelR = FSM_REV_SPEED;
        wheelL = FSM_REV_SPEED;
        nextState = BACKUP;
      }
      // else if((fabs(currentTiltFB)>2.5)||(fabs(currentTiltRL)>2.5)) {
      //   // Tilt sensor triggered - opponent trying to lift the robot?
      //   // Keep moving then spin immediately
      //   wheelR = FSM_FWD_SPEED;
      //   wheelL = FSM_FWD_SPEED;
      //   nextState = SPIN;
      // }
      else if(!fsmData.osFC && (fsmData.esFR | fsmData.esFL)) {
        // front edge sensor detected - brake immediately then start spin
        // TODO: check which sensors tripped and do whatever
        wheelR = 0;
        wheelL = 0;
        nextState = BACKUP;
      } 
      else if(fsmData.osFC && (esFR_latch & esFL_latch)) {
        // edge sensor detected - brake immediately then start spin
        // TODO: check which sensors tripped and do whatever
        wheelR = 0;
        wheelL = 0;
        nextState = BACKUP2;
      } 
      else {
        // drive forward
        wheelR = FSM_FWD_SPEED;
        wheelL = FSM_FWD_SPEED;
        // Vear towards an object in front not in center
        if(fsmData.osFR & !fsmData.osFL) wheelR *= 0.8;
        if(fsmData.osFL & !fsmData.osFR) wheelL *= 0.8;
      }
      break;

    case BACKUP: 
      if(stateChange) {
        // backup a bit
        fsmData.timer = millis()+FSM_BACKUP_TIME;
        setNeo(0,0,255); // BLUE
      }
      if(trig1) {
        // stop and idle when finger on FC
        nextState = IDLE0;
      }
      else if(millis()>=fsmData.timer) {
        nextState = SPIN;
      }
      else if(fsmData.esRR | fsmData.esRL) {
        // react to rear edge sensors by spinning
        nextState = SPIN;
      }
      else {
        // drive reverse
        wheelR = -FSM_REV_SPEED;
        wheelL = -FSM_REV_SPEED;
      }
      break;

    case SPIN: 
      if(stateChange) {
        // wait then stop spinning
        fsmData.timer = millis()+FSM_MAX_SPIN_TIME;
        fsmData.yaw0 = currentYaw;
        setNeo(150,0,150); // PURPLE
      }

      // spin away from edge before driving forward again
      wheelR = +fsmData.spinDir*FSM_SPIN_SPEED;
      wheelL = -fsmData.spinDir*FSM_SPIN_SPEED;

      if(trig1) {
        // stop and idle when finger on FC
        nextState = IDLE0;
      }
      else if(millis()>=fsmData.timer) {
        nextState = FWD;
      }
      else if(fabs(currentYaw - fsmData.yaw0) >= FSM_SPIN_ANGLE) {
        // stop spinning when spin angle achieved
        nextState = FWD;
      }
      else if(fsmData.osFC | fsmData.osFR | fsmData.osFL) {
        // stop spinning when an object is detected at front
        nextState = FWD;
      }
      break;

    case BACKUP2: 
      if(stateChange) {
        // backup a bit
        fsmData.timer = millis()+FSM_BACKUP_TIME;
        setNeo(0,0,255); // BLUE
      }
      if(trig1) {
        // stop and idle when finger on FC
        nextState = IDLE0;
      }
      else if(millis()>=fsmData.timer) {
        nextState = SPIN2;
      }
      else if(fsmData.esRR | fsmData.esRL) {
        // react to rear edge sensors by spinning
        nextState = SPIN;
      }
      else {
        // drive reverse
        wheelR = -FSM_REV_SPEED;
        wheelL = -FSM_REV_SPEED;
      }
      break;

    case SPIN2: 
      if(stateChange) {
        // wait then stop spinning
        fsmData.timer = millis()+FSM_MAX_SPIN_TIME;
        fsmData.yaw0 = currentYaw;
        setNeo(150,0,150); // PURPLE
      }

      // spin away from edge before driving forward again
      wheelR = +fsmData.spinDir*FSM_SPIN_SPEED;
      wheelL = -fsmData.spinDir*FSM_SPIN_SPEED;

      if(trig1) {
        // stop and idle when finger on FC
        nextState = IDLE0;
      }
      else if(millis()>=fsmData.timer) {
        nextState = FWD;
      }
      else if(fabs(currentYaw - fsmData.yaw0) >= FSM_SPIN_ANGLE) {
        // stop spinning when spin angle achieved
        nextState = FWD;
      }
      break;
    
    default: 
      setNeo(150,150,150); // WHITE
      // stop movement - freeze in unknown state until trigger
      wheelR = 0;
      wheelL = 0;
      if(trig1) {
        nextState = IDLE0;
      }
      break;
  }
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
void loop() {
  uint32_t t0 = millis();
  uint8_t range = 255;
  int16_t det = 0xFFFF;
  float vbat = 0.0;

  vbat = GetVbat();

  if(vbat<=VBAT_MIN && vbat>1.0 ) {
    // vbat<1 is DEBUG when no battery installed
    // remove power from sensors and motors
    // RP2040 still active
    // TODO: RP2040 lower power mode?
    Serial.printf("Vbat =  %f - shutting off sensors and motors", vbat);
    VregEnable(false);
    setNeo(50,0,0); // RED
    delay(1000);
    return;
  }

  det = ~GetIRdet(); // invert so that det bit value 1 = active
  GetTofData(); // update current range is new range is available
  range = currentRange;
  GetImuData();

  setFsmSensorData(range, det);

  float wheelR = 0.0;
  float wheelL = 0.0;

  fsm(wheelR, wheelL);

  MotorDrivePct(wheelL, wheelR);

  uint32_t t = millis()-t0;
  Serial.printf("%Ld: %f, %d, %f, %f, %04X, %f %f\n", 
    t, vbat, range, wheelR, wheelL, det&0x0F0F, currentYaw, currentTiltFB);

  delay(0);
}

//////////////////////////// CORE 2 ///////////////////////////////

void setup1() {
  while(!core1InitBasicsFinished) delay(1); /* atomic */

  // core2 code
  Core2_InitI2c();
  Core2_InitTof();
  Core2_InitImu(); // TODO: update code for core2
  core2InitFinished = true; /* atomic */
}

void loop1(){
  // calibrate IMU command from core1
  if(core2CalImu) {
    Core2_CalImuOffsets();
    core2CalImu = false;
  }

  // code to put in 2nd core
  Core2_GetTofSensor();
  Core2_ProcImu();
}

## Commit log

2025-11-29 added arduino and kicad support dirs
    [ms26.kicad_pcb, ms26.kicad_sch]
2025-12-09 seems to basically work with simple tests.. NO state machine to search etc...
    [FingerTech_Silver_Spark_223350.STEP, MS26-Body.3mf, MS26-MotorClampR.3mf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]
2025-12-09 Moved I2C and TOF sensors to core2 Goto object in rear Back up with small left or right turn when edge sensors tripped BUT currently stops when the edge is cleared. Need much more complex state machi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
2025-12-12 created a full feature FSM Uses TOF as start/stop switch by placing finger over the TOF hole in the front. When released the 5 sec timer starts before it runs. Travels from edge to edge spinning when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
    [MS26.FCStd]
2025-12-12 Added object sensing: SPIN stop spinning and attack FWD vear towards object using front left and righ sensors. FWD if fobject detected keep pushing until both front edge sensors trigger.
2025-12-13 3D created a lid for the top for the pennys weight. Implimented a wait 1sec filter for when a finger covers the TOF hole to start/stop the motion.
    [MS26-top.3mf, MS26-topCap.3mf, MS26.FCStd]
2025-12-13 added define for 1sec finger filter added hysterisis for finger detect reduced led intensity for sensor display and battery low
2025-12-15 Integrated rotation velocity to get a yaw value and sent from core2 to core1 Used yaw to measure spin angle
2025-12-15 Used IMU yaw data to SPIN a specifc angle instead of simply timed
2025-12-16 Added tilt and hit sensing data in buffer from core2 to core1 Attempted to use tilt forward sensing to detetct competitor lifting the front. But had to set it to 10deg bcause of noisy IMU data I gues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
2025-12-16 "Fixed" humping issue when opponent is pushed off the arena
    [ms26.ino]
2025-12-16 Stop when 3 or 4 edge sensors tripped - must not be on the arena black
